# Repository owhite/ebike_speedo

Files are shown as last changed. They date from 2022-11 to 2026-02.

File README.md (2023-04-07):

# EBIKE SPEEDOMETER FEATURES
* Completely uninteresting 14 segment LED displays
* Serial data --> board --> BLE to smartphone
* Compatible with [MESC controller](https://github.com/davidmolony/MESC_Firmware)

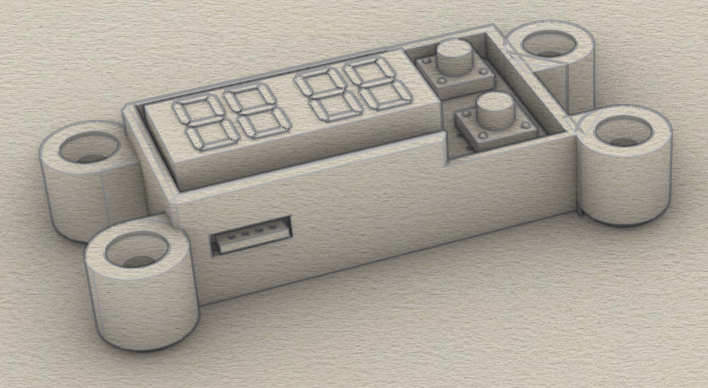
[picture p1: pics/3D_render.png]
3D speedometer


## Operation
Device connects to an ESC (e.g. the [MP2](https://github.com/badgineer/CCC_ESC) with a [F405 pill](https://github.com/davidmolony/F405_pill)) and receives json data via a serial output. Typcial data stream could include:
```
{"amps": 10, "volts": 20, "rpm": 200, "temp": 90}
```
But you can configure the F405 to send other values, but the speedometer is expecting the above tags and ignores others. The speedometer uses these values as ints that will be displayed on the 14 segment LED. RPM will be converted to MPH prior to display. 

Regardless of the values or data structure received, the entired data stream is passed on to a bluetooth device which can be captured on your smartphone using an app like [Serial Bluetooth Terminal](https://play.google.com/store/apps/details?id=de.kai_morich.serial_bluetooth_terminal). 

## Programming
* Use the [STM32CubeIDE](https://www.st.com/en/development-tools/stm32cubeide.html) to progam the microcontroller on the ESC
* Use [platformio](https://platformio.org/) for the ESP32. 

## ESP32 quirks
There are conflicts between bootstrapping capability and usage of some pins. If you notice your board wont program unless you keep the button depressed, it might be due to this conflict.

This reqiures that you burn the flash voltage selection eFuses change the internal regulator’s output voltage to 3.3 V. This was fixed with using a tool from [espressif](https://docs.espressif.com/projects/esptool/en/latest/esp32s3/espefuse/index.html): 

```
$ espefuse.py set_flash_voltage 3.3V --port /dev/cu.usbserial-01562A86
```
be sure to use the appropriate port name. 

## Speedometer operation
* Assemble PCB
* Set the following parameters in ESP32 code:
```
#define POLEPAIRS    5
#define CIRCUMFERENCE 78.5 // circumference in cm of wheel
#define MAXTEMP 65 
// for the range when it provides a percentage
#define MINVOLTAGE 86.4    // lower bound of voltage
#define MAXVOLTAGE 104.0   // 24s lipos fully charge

```
* Upload code to ESP32 using platformio
* Press top button to change LED display
* Display shows: "M", "A", "V" "T" for MPH, amps, battery voltage, and temperature
* Find "ESP32 Speedometer" on your smartphone
* Gather data using an app like [Serial Bluetooth Terminal](https://play.google.com/store/apps/details?id=de.kai_morich.serial_bluetooth_terminal)
* Note on the json data there's a mS value, press lower button to reset to zero

## BOM
* Adafruit Quad Alphanumeric Display w/ backpack
* Adafruit HUZZAH32 – ESP32 Feather Board
* PCB (gerbers are [here](V1.1/gerbers))
* Two 10k 0805 resistors
* [TS14-1212-70-BK-160-SCR-D](https://www.cuidevices.com/product/resource/ts14.pdf) tactile switches
* 0.1 inch spacing header boards
* This [housing](3D_model/speedo_housing.stl) might be useful

Let's play: how tall is your stack of boards!? 
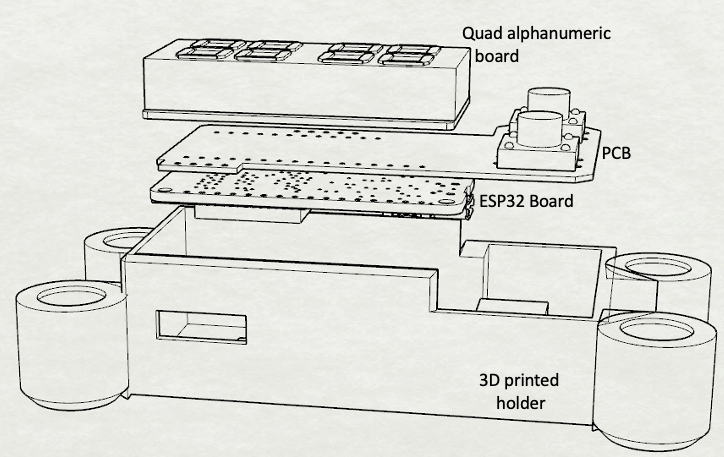
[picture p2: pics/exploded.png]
Separate parts


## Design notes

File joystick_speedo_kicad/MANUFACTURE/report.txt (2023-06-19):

Info: Placement file: '/Users/owhite/kicad/ebike_speedo/speed_joystick/speed_joystick-all-pos.csv'.
Info: Component count: 20.
Info: File generation successful.

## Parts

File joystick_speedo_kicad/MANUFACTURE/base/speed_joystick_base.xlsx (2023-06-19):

Comment | Designator | Footprint | LCSC
10k | R1,R2,R3,R4,R5,R6,R9,R10 | Resistor_SMD:R_0805_2012Metric | C25804
120 | R7 | Resistor_SMD:R_0805_2012Metric | C17437
JS5208 | SW1 | JS5208:SW_JS5208 | C3029619
TJA1050T/CM,118 | U2 | Package_SO:SOIC-8_3.9x4.9mm_P1.27mm | C6952

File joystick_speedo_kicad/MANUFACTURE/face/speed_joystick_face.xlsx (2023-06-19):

Comment | Designator | Footprint | LCSC
0.1uF | C1,C2,C3,C4,C5,C6,C7,C8,C9,C10,C11,C12,C13,C14,C15,C16,C17,C18,C19,C20,C21,C22,C23,C24,C25,C26 | Capacitor_SMD:C_0603_1608Metric | C28233
1uF | C27,C28 | Capacitor_SMD:C_0603_1608Metric | C15849
10uF | C29,C30 | Capacitor_SMD:C_0603_1608Metric | C96446
SK6812 | D1,D2,D3,D4,D5,D6,D7,D8,D9,D10,D11,D12,D13,D14,D15,D16,D17,D18,D19,D20,D21,D22,D23,D24 | LED_SMD:LED-SMD_4P-L4.0-W1.6-L | C2890037
100k | R8 | Resistor_SMD:R_0805_2012Metric | C25803
TXS0108E | U3 | Package_SO:TSSOP-20_4.4x6.5mm_P0.65mm | C17206
XC6206PxxxMR | U4 | Package_TO_SOT_SMD:SOT-23 | C5446

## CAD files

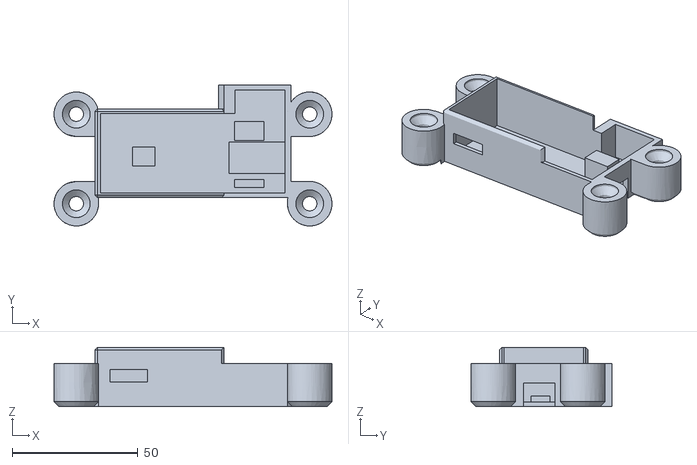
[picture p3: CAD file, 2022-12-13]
3D_model/speedo_housing.stl
110.8 x 56.2 x 23.7

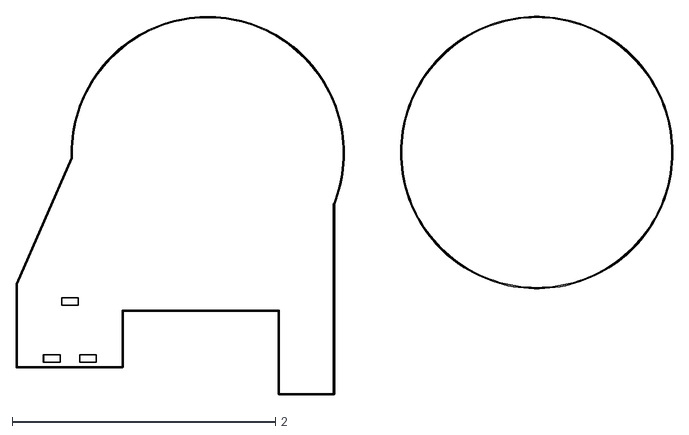
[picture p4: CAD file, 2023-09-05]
joystick_speedo_kicad/DXFs/speed_joystick-Edge_Cuts.dxf
4.99 x 2.87

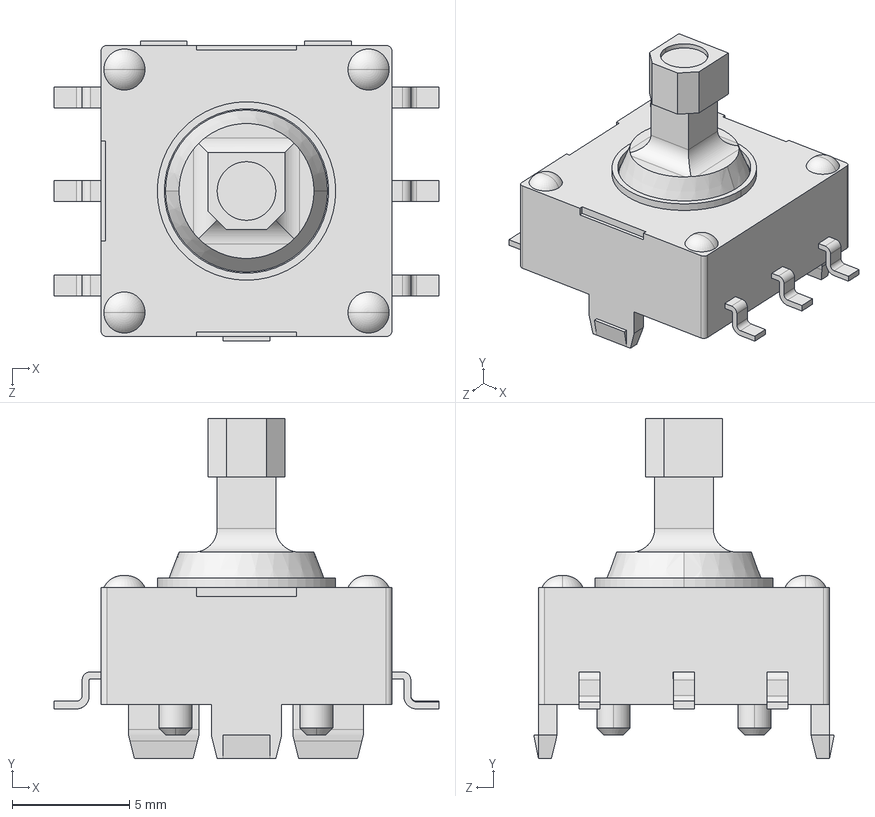
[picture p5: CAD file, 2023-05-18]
mechanical_speedo/JS5208/JS5208.step
16.4 x 14.5 x 12.8 mm

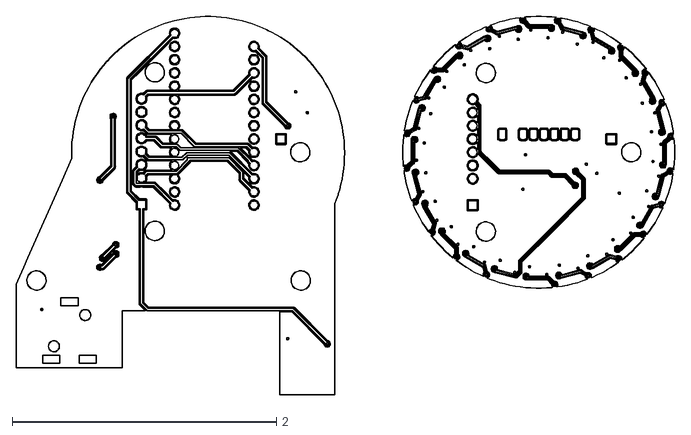
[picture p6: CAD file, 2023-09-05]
joystick_speedo_kicad/DXFs/speed_joystick-B_Cu.dxf
4.98 x 2.86

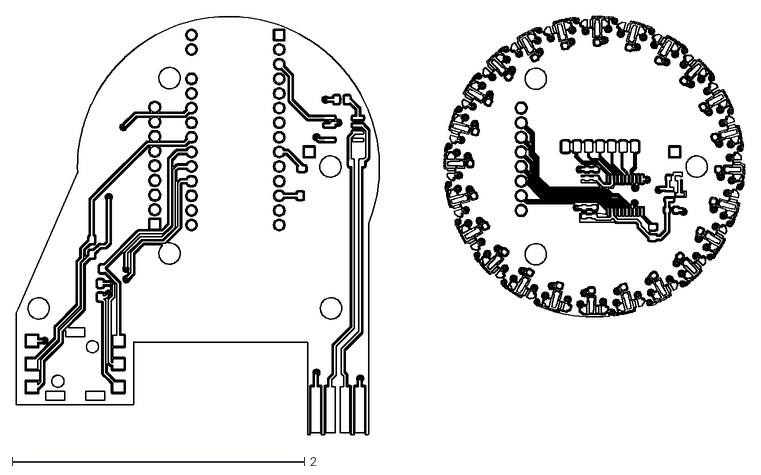
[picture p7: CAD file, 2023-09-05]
joystick_speedo_kicad/DXFs/speed_joystick-F_Cu.dxf
4.98 x 2.86

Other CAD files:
joystick_speedo_kicad/DXFs/speed_joystick-B_Mask.dxf
joystick_speedo_kicad/DXFs/speed_joystick-B_Paste.dxf
joystick_speedo_kicad/DXFs/speed_joystick-B_Silkscreen.dxf
joystick_speedo_kicad/DXFs/speed_joystick-F_Mask.dxf
joystick_speedo_kicad/DXFs/speed_joystick-F_Paste.dxf
joystick_speedo_kicad/DXFs/speed_joystick-F_Silkscreen.dxf

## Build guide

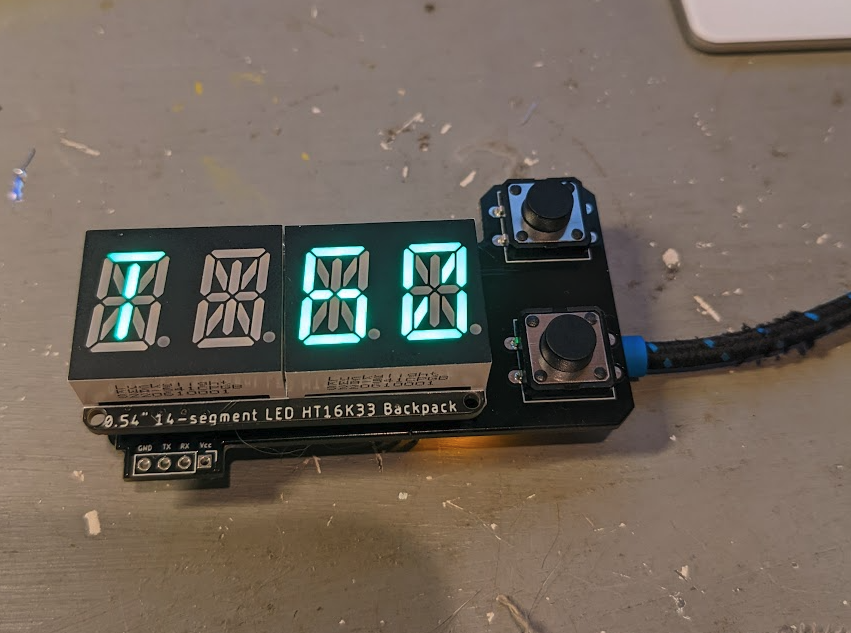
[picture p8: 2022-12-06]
pics/assembled.png

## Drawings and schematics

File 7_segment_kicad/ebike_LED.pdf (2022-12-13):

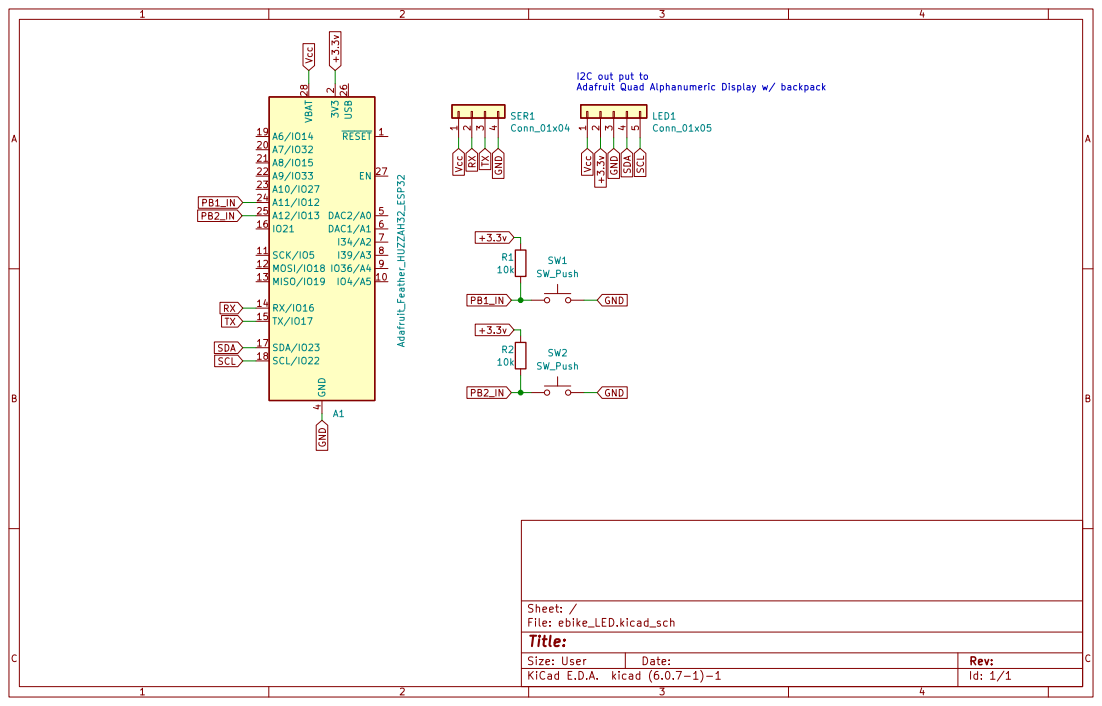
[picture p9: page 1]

I2C out put to
Adafruit Quad Alphanumeric Display w/ backpack

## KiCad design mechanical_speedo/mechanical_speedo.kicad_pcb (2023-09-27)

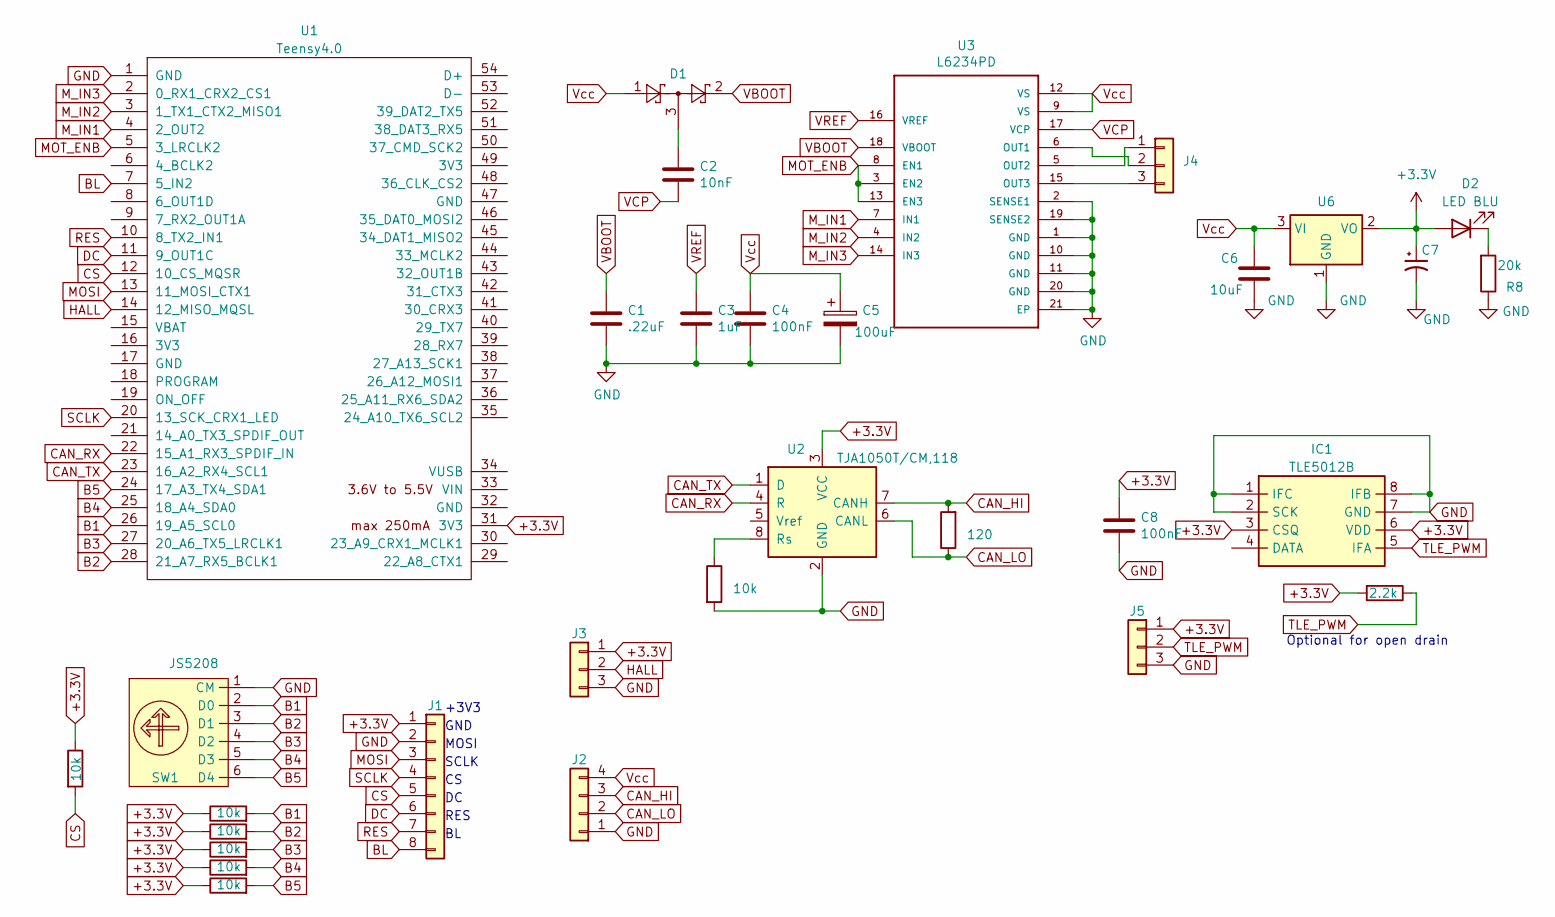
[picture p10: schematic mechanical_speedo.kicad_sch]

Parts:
C1: .22uF; C_0805_2012Metric; LCSC C5378
C2: 10nF; C_0603_1608Metric; LCSC C57112
C3: 1uF; C_0805_2012Metric; LCSC C28323
C4, C8: 100nF; C_0603_1608Metric; LCSC C14663
C5: 100uF; CP_EIA-3528-21_Kemet-B; LCSC C16133
C6: 10uF; C_0805_2012Metric; LCSC C15850
C7: C_Polarized_Small_US; CP_EIA-3216-18_Kemet-A; LCSC C7171
D1: BAT54S; SOT-23; LCSC C19726
D2: LED BLU; LED_0603_1608Metric; LCSC C72041
IC1: TLE5012B; SOIC127P600X175-8N; Mouser Part Number 726-TLE5012BE5000X
J1: Conn_01x08; 8_hole
J2: Conn_01x04; my_4_tab_edge
J3, J4, J5: Conn_01x03; PinHeader_1x03_P2.54mm_Vertical
R1, R2, R3, R4, R5, R6, R9: 10k; R_0805_2012Metric; LCSC C25804
R7: 120; R_0805_2012Metric; LCSC C17437
R8: 20k; R_0603_1608Metric; LCSC C4184
R11: 2.2k; R_0603_1608Metric; LCSC C4184
SW1: JS5208; SW_JS5208; LCSC C3029619
U1: Teensy4.0; Teensy32
U2: TJA1050T/CM,118; SOIC-8_3.9x4.9mm_P1.27mm; LCSC C6952
U3: L6234PD
U6: LD1117S18TR_SOT223; SOT-223-3_TabPin2; LCSC C2984862

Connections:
+3.3V: C7.1, C8.1, D2.2 (A), IC1.3 (CSQ), IC1.6 (VDD), J1.1, J3.1, J5.1, R1.1, R2.1, R4.1, R5.1, R6.1, R9.1, R11.2, U1.31 (3V3), U2.3 (VCC), U6.2 (VO)
B1: R6.2, SW1.2 (D0), U1.26 (19_A5_SCL0)
B2: R5.2, SW1.3 (D1), U1.28 (21_A7_RX5_BCLK1)
B3: R4.2, SW1.4 (D2), U1.27 (20_A6_TX5_LRCLK1)
B4: R2.2, SW1.5 (D3), U1.25 (18_A4_SDA0)
B5: R1.2, SW1.6 (D4), U1.24 (17_A3_TX4_SDA1)
BL: J1.8, U1.7 (5_IN2)
CAN_HI: J2.3, R7.2, U2.7 (CANH)
CAN_LO: J2.2, R7.1, U2.6 (CANL)
CAN_RX: U1.22 (15_A1_RX3_SPDIF_IN), U2.4 (R)
CAN_TX: U1.23 (16_A2_RX4_SCL1), U2.1 (D)
CS: J1.5, R9.2, U1.12 (10_CS_MQSR)
DC: J1.6, U1.11 (9_OUT1C)
GND: C1.2, C3.2, C4.2, C5.2, C6.2, C7.2, C8.2, IC1.1 (IFC), IC1.2 (SCK), IC1.7 (GND), IC1.8 (IFB), J1.2, J2.1, J3.3, J5.3, R3.2, R8.1, SW1.1 (CM), U1.1 (GND), U2.2 (GND), U3.1 (GND), U3.2 (SENSE1), U3.10 (GND), U3.11 (GND), U3.19 (SENSE2), U3.20 (GND), U3.21 (EP), U6.1 (GND)
HALL: J3.2, U1.14 (12_MISO_MQSL)
MOSI: J1.3, U1.13 (11_MOSI_CTX1)
MOT_ENB: U1.5 (3_LRCLK2), U3.3 (EN2), U3.8 (EN1), U3.13 (EN3)
M_IN1: U1.4 (2_OUT2), U3.7 (IN1)
M_IN2: U1.3 (1_TX1_CTX2_MISO1), U3.4 (IN2)
M_IN3: U1.2 (0_RX1_CRX2_CS1), U3.14 (IN3)
unnamed: C2.1, D1.3
unnamed: D2.1 (K), R8.2
unnamed: J4.1, U3.5 (OUT2)
unnamed: J4.2, U3.6 (OUT1)
unnamed: J4.3, U3.15 (OUT3)
unnamed: R3.1, U2.8 (Rs)
RES: J1.7, U1.10 (8_TX2_IN1)
SCLK: J1.4, U1.20 (13_SCK_CRX1_LED)
TLE_PWM: IC1.5 (IFA), J5.2, R11.1
VBOOT: C1.1, D1.2, U3.18 (VBOOT)
VCP: C2.2, U3.17 (VCP)
VREF: C3.1, U3.16 (VREF)
Vcc: C4.1, C5.1, C6.1, D1.1, J2.4, U3.9 (VS), U3.12 (VS), U6.3 (VI)

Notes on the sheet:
MOSI
Optional for open drain
RES
GND
+3V3
SCLK

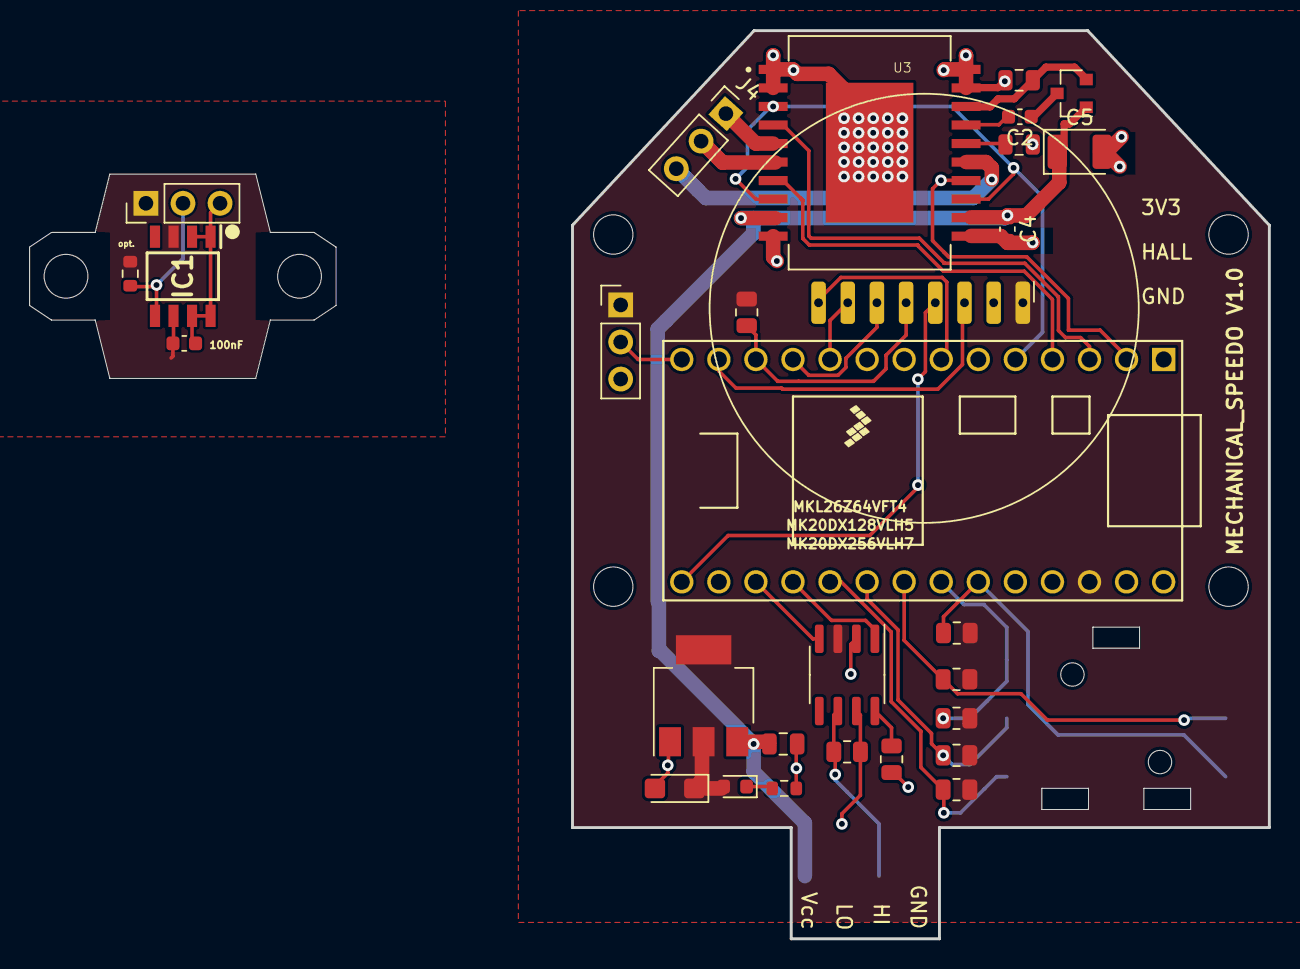
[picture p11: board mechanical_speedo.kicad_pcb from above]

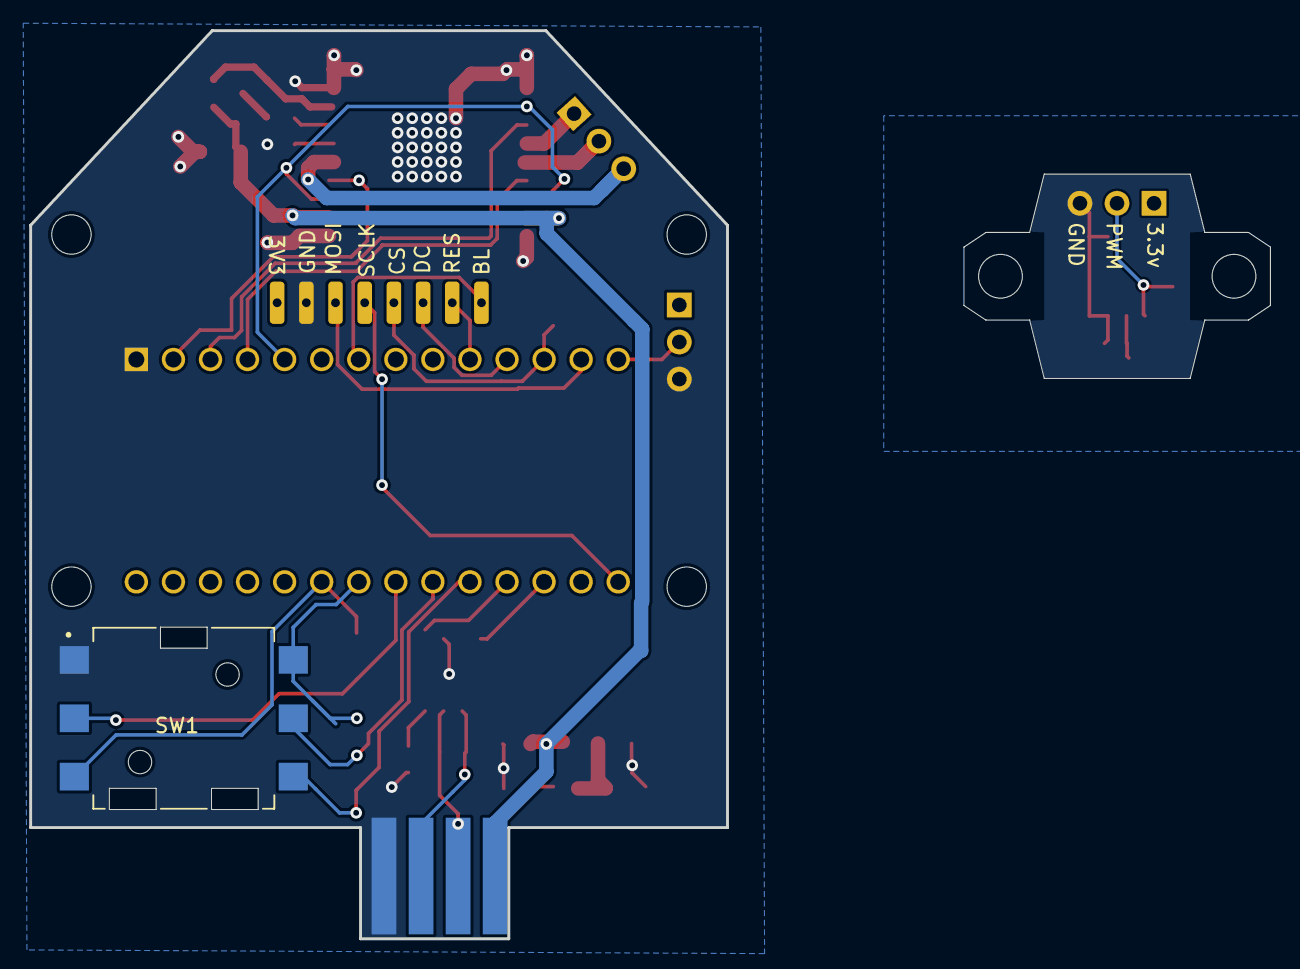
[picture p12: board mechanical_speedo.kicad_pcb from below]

Board: 2 copper layers, 47.8 x 62.2 mm, 31 parts (2 on the bottom side), 33 nets.

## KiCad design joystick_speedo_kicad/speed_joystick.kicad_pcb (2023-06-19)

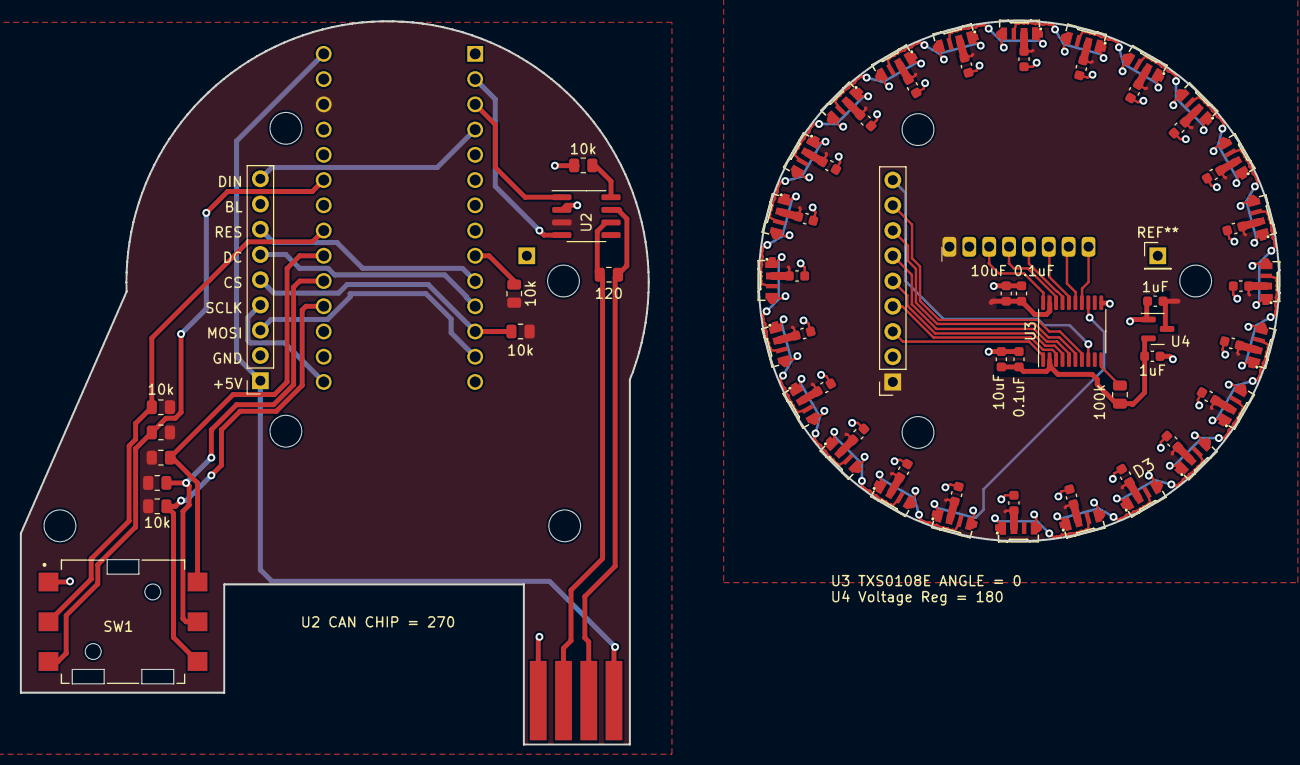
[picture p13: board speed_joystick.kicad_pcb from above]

Board: 2 copper layers, 52.4 x 52.4 mm, 73 parts (1 on the bottom side), 62 nets.

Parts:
C1, C2, C3, C4, C5, C6, C7, C8, C9, C10, C11, C12, C13, C14, C15, C16, C17, C18, C19, C20, C21, C22, C23, C24, C25, C26: 0.1uF; C_0603_1608Metric
C27, C28: 1uF; C_0603_1608Metric
C29, C30: 10uF; C_0603_1608Metric
D1, D2, D3, D4, D5, D6, D7, D8, D9, D10, D11, D12, D13, D14, D15, D16, D17, D18, D19, D20, D21, D22, D23, D24: SK6812; LED-SMD_4P-L4.0-W1.6-L
J1: Conn_01x08; 8_hole
J2: Conn_01x04; my_4_tab_edge
J3, J4: Conn_01x09; PinSocket_1x09_P2.54mm_Vertical
R1, R2, R3, R4, R5, R6, R9, R10: 10k; R_0805_2012Metric
R7: 120; R_0805_2012Metric
R8: 100k; R_0805_2012Metric
SW1: JS5208; SW_JS5208
U1: Teensy3.2; Teensy32
U2: TJA1050T/CM,118; SOIC-8_3.9x4.9mm_P1.27mm
U3: TXS0108E; TSSOP-20_4.4x6.5mm_P0.65mm
U4: XC6206PxxxMR; SOT-23

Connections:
+3.3V: R1.1, R2.1, R4.1, R5.1, R6.1, R9.1, R10.1, U1.31 (3.3V), U2.3 (VCC)
+5V: J2.4, J4.1, U1.33 (Vin)
B1: R6.2, SW1.2 (D0), U1.26 (19_A5_SCL0_Touch)
B2: R5.2, SW1.3 (D1), U1.28 (21_A7_RX1_CS_PWM)
B3: R4.2, SW1.4 (D2), U1.25 (18_A4_SDA0_Touch)
B4: R2.2, SW1.5 (D3), U1.24 (17_A3_SDA0_Touch)
B5: R1.2, SW1.6 (D4), U1.23 (16_A2_SCL0_Touch)
BL: J4.8, U1.7 (5_TX1_PWM)
CAN_HI: J2.3, R7.2, U2.7 (CANH)
CAN_LO: J2.2, R7.1, U2.6 (CANL)
CAN_RX: U1.2 (0_RX1_Touch), U2.4 (R)
CAN_TX: U1.3 (1_TX1_Touch), U2.1 (D)
CS1: J4.5, R9.2, U1.12 (10_TX2_CS_PWM)
CS2: R10.2, U1.9 (7_RX3_DOUT)
DC: J4.6, U1.11 (9_RX2_CS_PWM)
DIN: J4.9, U1.4 (2)
DIN_SIG: D24.1 (DIN), U3.13 (B7)
GND: J2.1, J4.2, R3.2, SW1.1 (CM), U1.1 (GND), U2.2 (GND)
MOSI: J4.3, U1.13 (11_DOUT)
unnamed: D1.1 (DIN), D2.3 (DOUT)
unnamed: D2.1 (DIN), D3.3 (DOUT)
unnamed: D3.1 (DIN), D4.3 (DOUT)
unnamed: D4.1 (DIN), D5.3 (DOUT)
unnamed: D5.1 (DIN), D6.3 (DOUT)
unnamed: D6.1 (DIN), D7.3 (DOUT)
unnamed: D7.1 (DIN), D8.3 (DOUT)
unnamed: D8.1 (DIN), D9.3 (DOUT)
unnamed: D10.1 (DIN), D11.3 (DOUT)
unnamed: D9.1 (DIN), D10.3 (DOUT)
unnamed: D11.1 (DIN), D12.3 (DOUT)
unnamed: D12.1 (DIN), D13.3 (DOUT)
unnamed: D13.1 (DIN), D14.3 (DOUT)
unnamed: D14.1 (DIN), D15.3 (DOUT)
unnamed: D15.1 (DIN), D16.3 (DOUT)
unnamed: D16.1 (DIN), D17.3 (DOUT)
unnamed: D17.1 (DIN), D18.3 (DOUT)
unnamed: D18.1 (DIN), D19.3 (DOUT)
unnamed: D19.1 (DIN), D20.3 (DOUT)
unnamed: D20.1 (DIN), D21.3 (DOUT)
unnamed: D21.1 (DIN), D22.3 (DOUT)
unnamed: D22.1 (DIN), D23.3 (DOUT)
unnamed: D23.1 (DIN), D24.3 (DOUT)
unnamed: J1.3, U3.20 (B1)
unnamed: J1.4, U3.18 (B2)
unnamed: J1.5, U3.17 (B3)
unnamed: J1.6, U3.16 (B4)
unnamed: J1.7, U3.15 (B5)
unnamed: J1.8, U3.14 (B6)
unnamed: R3.1, U2.8 (Rs)
unnamed: R8.2, U3.10 (OE)
RES: J4.7, U1.10 (8_TX3_DIN)
R_+3.3V: C25.1, C27.1, C30.1, R8.1, U3.2 (VCCA), U4.2 (VO)
R_+5V: C1.1, C2.1, C3.1, C4.1, C5.1, C6.1, C7.1, C8.1, C9.1, C10.1, C11.1, C12.1, C13.1, C14.1, C15.1, C16.1, C17.1, C18.1, C19.1, C20.1, C21.1, C22.1, C23.1, C24.1, C26.1, C28.1, C29.1, D1.2 (VDD), D2.2 (VDD), D3.2 (VDD), D4.2 (VDD), D5.2 (VDD), D6.2 (VDD), D7.2 (VDD), D8.2 (VDD), D9.2 (VDD), D10.2 (VDD), D11.2 (VDD), D12.2 (VDD), D13.2 (VDD), D14.2 (VDD), D15.2 (VDD), D16.2 (VDD), D17.2 (VDD), D18.2 (VDD), D19.2 (VDD), D20.2 (VDD), D21.2 (VDD), D22.2 (VDD), D23.2 (VDD), D24.2 (VDD), J1.1, J3.1, U3.19 (VCCB), U4.3 (VI)
R_BL: J3.8, U3.7 (A6)
R_CS: J3.5, U3.4 (A3)
R_DC: J3.6, U3.5 (A4)
R_DIN: J3.9, U3.8 (A7)
R_GND: C1.2, C2.2, C3.2, C4.2, C5.2, C6.2, C7.2, C8.2, C9.2, C10.2, C11.2, C12.2, C13.2, C14.2, C15.2, C16.2, C17.2, C18.2, C19.2, C20.2, C21.2, C22.2, C23.2, C24.2, C25.2, C26.2, C27.2, C28.2, C29.2, C30.2, D1.4 (VSS), D2.4 (VSS), D3.4 (VSS), D4.4 (VSS), D5.4 (VSS), D6.4 (VSS), D7.4 (VSS), D8.4 (VSS), D9.4 (VSS), D10.4 (VSS), D11.4 (VSS), D12.4 (VSS), D13.4 (VSS), D14.4 (VSS), D15.4 (VSS), D16.4 (VSS), D17.4 (VSS), D18.4 (VSS), D19.4 (VSS), D20.4 (VSS), D21.4 (VSS), D22.4 (VSS), D23.4 (VSS), D24.4 (VSS), J1.2, J3.2, U3.11 (GND), U4.1 (GND)
R_MOSI: J3.3, U3.1 (A1)
R_RES: J3.7, U3.6 (A5)
R_SCLK: J3.4, U3.3 (A2)
SCLK: J4.4, U1.20 (13_LED_SCK)

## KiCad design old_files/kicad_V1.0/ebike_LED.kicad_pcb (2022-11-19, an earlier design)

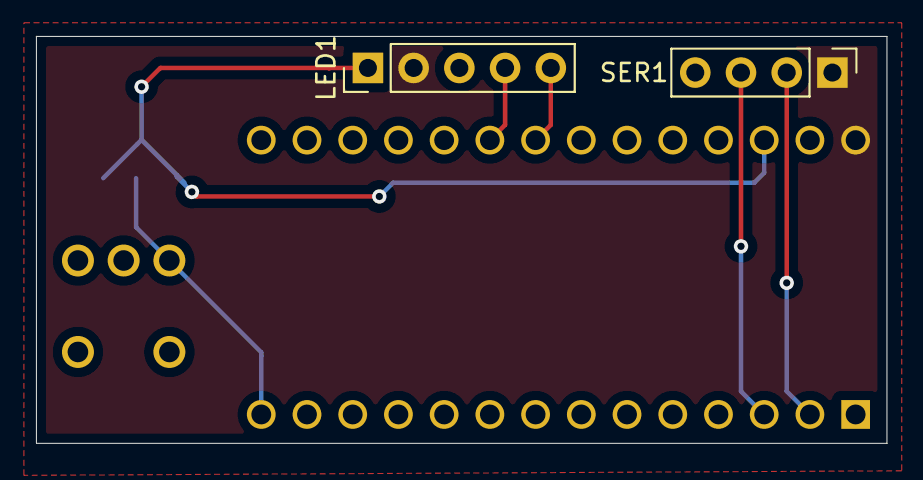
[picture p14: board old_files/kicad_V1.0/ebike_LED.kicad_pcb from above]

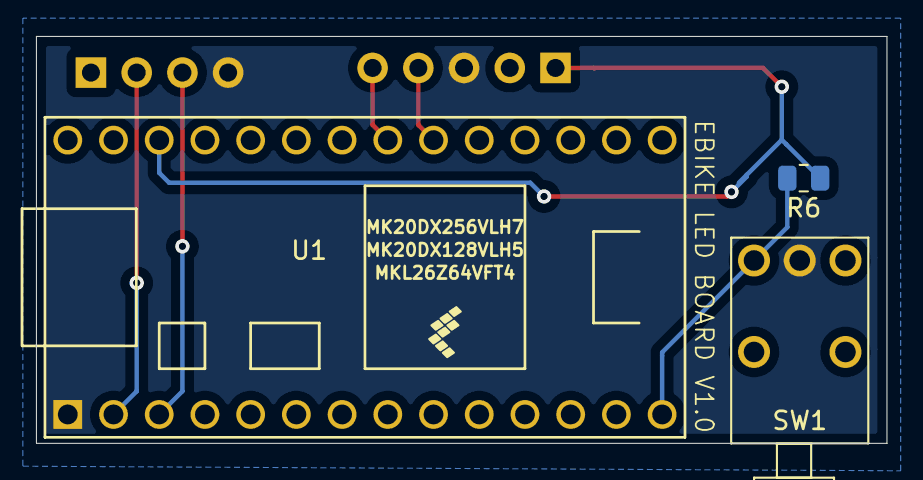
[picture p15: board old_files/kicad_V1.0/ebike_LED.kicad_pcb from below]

Board: 2 copper layers, 47.2 x 22.6 mm, 5 parts (3 on the bottom side), 8 nets.

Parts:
LED1: Conn_01x05; PinHeader_1x05_P2.54mm_Vertical
R6: 10k; R_0805_2012Metric
SER1: Conn_01x04; PinHeader_1x04_P2.54mm_Vertical
SW1: Conn_01x02; my_pushbutton
U1: Teensy3.2; Teensy32

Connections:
+3.3v: LED1.1, R6.1, U1.31
GND: LED1.3, SER1.4, SW1.2, U1.1
PB1_IN: R6.2, SW1.1, U1.14
Rx-BESC: SER1.3, U1.3
SCL: LED1.5, U1.26
SDA: LED1.4, U1.25
Tx-BESC: SER1.2, U1.2
Vcc: LED1.2, SER1.1, U1.33

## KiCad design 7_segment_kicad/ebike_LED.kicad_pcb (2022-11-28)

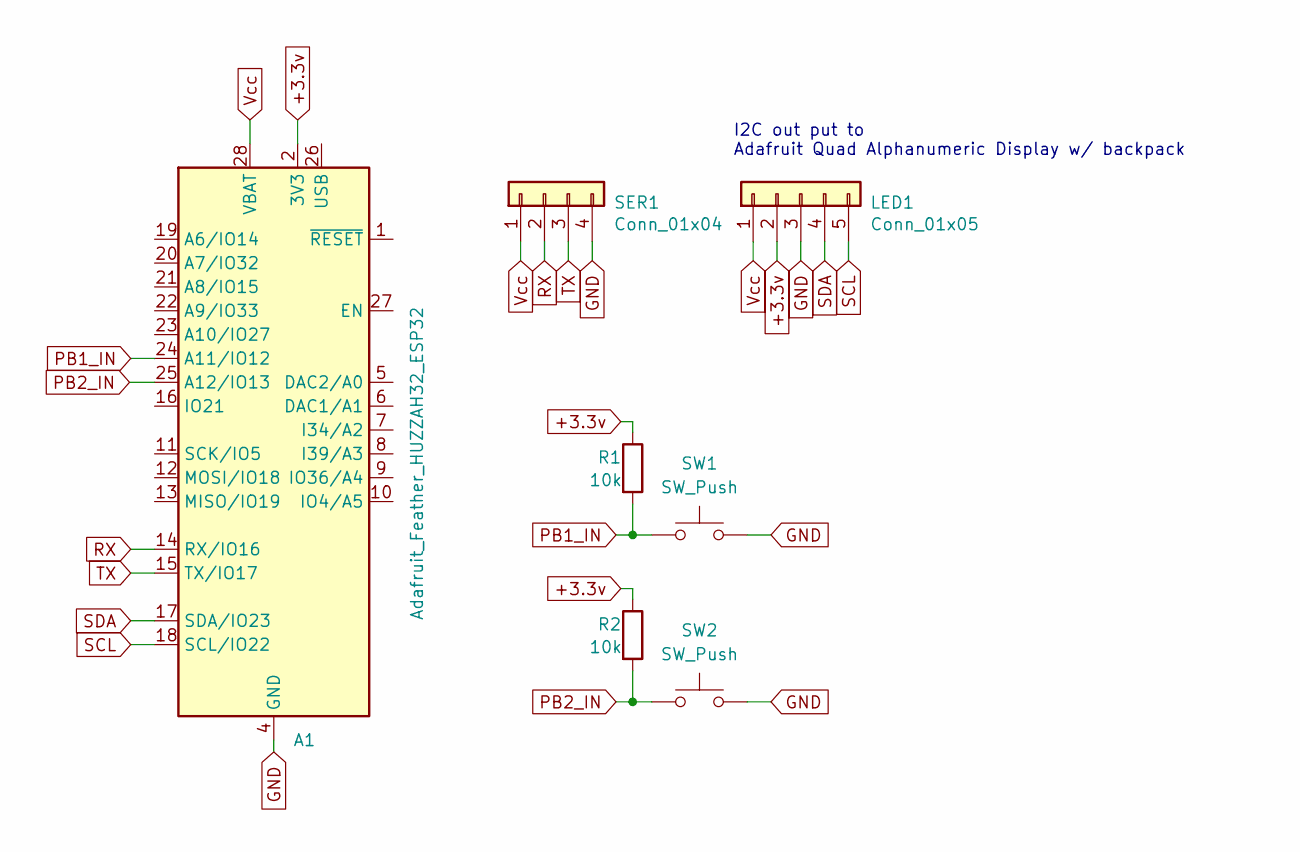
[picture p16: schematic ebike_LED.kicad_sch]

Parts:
A1: Adafruit_Feather_HUZZAH32_ESP32; Adafruit_Feather
LED1: Conn_01x05; PinHeader_1x05_P2.54mm_Vertical
R1, R2: 10k; R_0805_2012Metric
SER1: Conn_01x04; PinHeader_1x04_P2.54mm_Vertical
SW1, SW2: SW_Push; SW_PUSH-12mm

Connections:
+3.3v: A1.2 (3V3), LED1.2, R1.1, R2.1
GND: A1.4 (GND), LED1.3, SER1.4, SW1.2, SW2.2
PB1_IN: A1.24 (A11/IO12), R1.2, SW1.1
PB2_IN: A1.25 (A12/IO13), R2.2, SW2.1
RX: A1.14 (RX/IO16), SER1.2
SCL: A1.18 (SCL/IO22), LED1.5
SDA: A1.17 (SDA/IO23), LED1.4
TX: A1.15 (TX/IO17), SER1.3
Vcc: A1.28 (VBAT), LED1.1, SER1.1

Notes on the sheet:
I2C out put to Adafruit Quad Alphanumeric Display w/ backpack

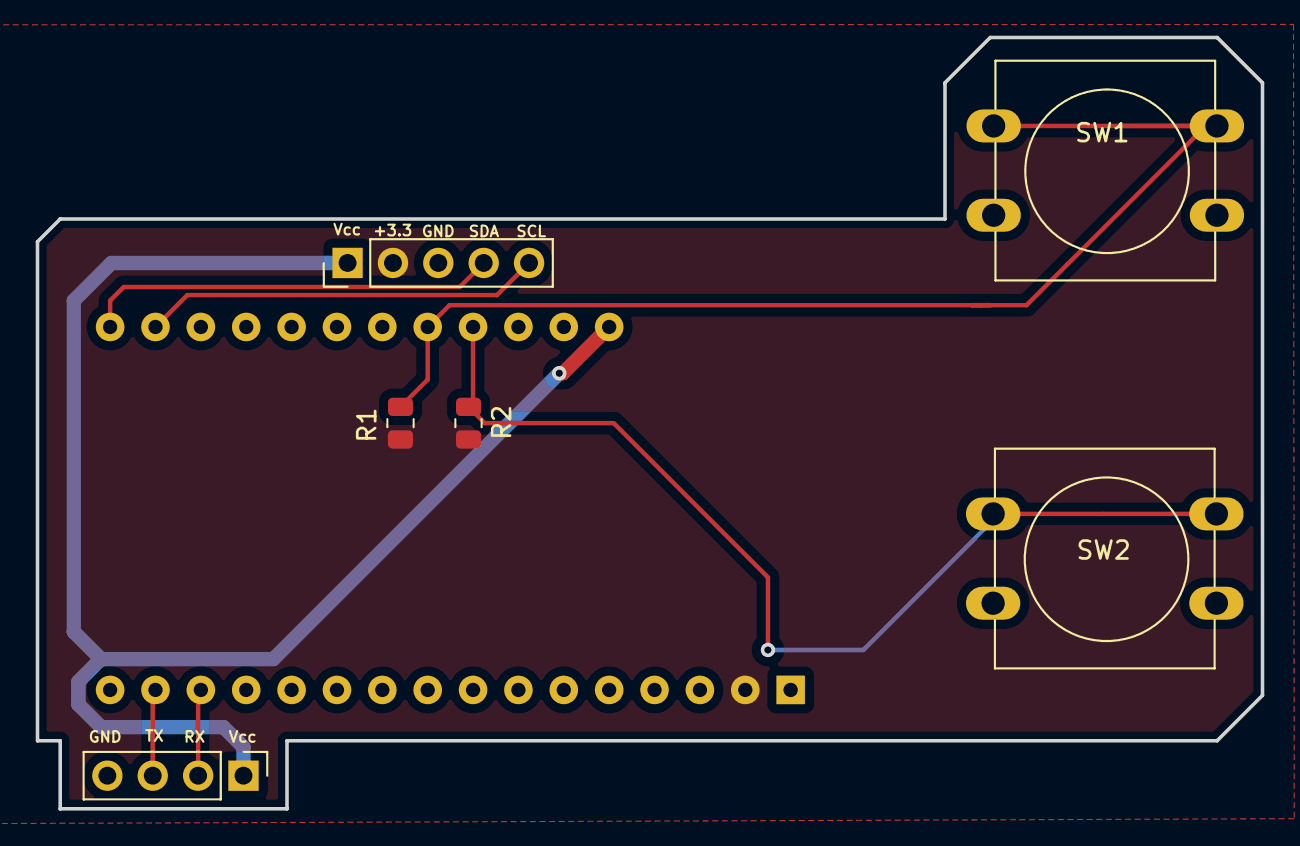
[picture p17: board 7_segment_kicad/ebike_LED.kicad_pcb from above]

Board: 2 copper layers, 68.6 x 43.2 mm, 7 parts (1 on the bottom side), 9 nets.

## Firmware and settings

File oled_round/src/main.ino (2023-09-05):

// Libraries required to make this thing run.
//  respect all licensing associated with these libraries:
#include <FlexCAN_T4.h>
#include <MenuSystem.h> 
#include <Adafruit_GFX.h>
#include <Adafruit_GC9A01A.h>
#include <Adafruit_NeoPixel.h>
#include <DigiFont.h>
#include <EEPROM.h>
// Other custom code blocks
#include <display_handling.h> // my collection of stupid things
#include <menu_handling.h>
#include <bitmaps.h>
#include <MESCerror.h>
#include <states.h>
#include <can_ids.h> // from Jens' code

// BIKE setup, no I'm not storing all this in eeprom
#define BIKE_SPEED_MAX 50
#define POLEPAIRS    7
#define CIRCUMFERENCE 219.5 
#define GEAR_RATIO 9.82
#define CM_IN_MILE 160900
#define MINVOLTAGE 40.0
#define MAXVOLTAGE 60.0
#define MAXTEMP 70
#define MAXSPEED 50
float EHZ_SCALE_M = (CIRCUMFERENCE * 60 * 60) / (CM_IN_MILE * GEAR_RATIO * POLEPAIRS);
float EHZ_SCALE_K = (CIRCUMFERENCE * 60 * 60) / (100000 * GEAR_RATIO * POLEPAIRS);

// eeprom storage positions
#define RESET_STORED_VALUES 0x0000 // change to 1 if store new values
#define PIX_BRIGHTNESS_ADDR 0x0011
#define PIX_COLOR_ADDR      0x0012
#define DISPLAY_STATE_ADDR  0x0013
#define METRIC_PREF_ADDR    0x0014

// joystick button setup
const uint8_t btnMax = 5;
elapsedMillis elapsedBtnTime[btnMax] = {elapsedMillis(), elapsedMillis(), elapsedMillis(), elapsedMillis(), elapsedMillis()};
uint16_t btnDelay = 50;
boolean btnPressed[] = {false, false, false, false, false};
uint8_t btnPin[5] = {19, 21, 18, 17, 16};
uint8_t btnNum = 0;

// neopixel setup
#define PIXELPIN   2
#define NUMPIXELS 24
Adafruit_NeoPixel ring(NUMPIXELS, PIXELPIN, NEO_GRB + NEO_KHZ800);

const uint8_t PIX_RED   = 0;
const uint8_t PIX_GREEN = 1;
const uint8_t PIX_BLUE  = 2;
const uint8_t PIX_WHITE = 3; 

uint32_t colorArray[] = {ring.Color(255, 0, 0), ring.Color(0, 255, 0), ring.Color(0, 0, 255), ring.Color(255, 255, 255)};

// gets changed later by eepromDefaultValues();
uint8_t metric_pref = 0;
uint8_t pixelColor = PIX_WHITE;
uint8_t neoBrightVal = 5;

// round oled setup
//  see Adafruit_GC9A01A github for pin usage
#define LCD_BL_PIN 5 // pin used for brightness
Adafruit_GC9A01A lcd(10, 9, 11, 13, 8, 12);

// CAN stuff
#define CAN_PACKET_SIZE  8

FlexCAN_T4<CAN2, RX_SIZE_256, TX_SIZE_16> can;
CAN_message_t msg;
unsigned long canReceiveTime;
const unsigned long canInterval = 2000;
uint8_t canBuf[8] = {};
const uint8_t userRequestMax = 5; 
float reportedValue; 
float reportValues[userRequestMax] = {};
bool canFlag = false;
bool errorFlag = false;
bool canFlag_old = false;
bool errorFlag_old = false;

// Digifont setup, set up here but used in displayHandlder object. 
void customLineH(int x0,int x1, int y, int c)    { lcd.drawFastHLine(x0,y,x1-x0+1,c); }
void customLineV(int x, int y0,int y1, int c)    { lcd.drawFastVLine(x,y0,y1-y0+1,c); } 
void customRect(int x, int y,int w,int h, int c) { lcd.fillRect(x,y,w,h,c); } 
DigiFont font(customLineH, customLineV, customRect);

// display things
int input_state = INPUT_MENU;
int state = IDLE_DISPLAY;

displayHandler display;

uint32_t dataInterval = 4000; 
int main_display_state = MAIN_DISPLAY_BAT;
uint8_t brightness_val = 10;
int count = 0;
bool entered_menu = true;
float level_old = 0.0;
float level = 0.8;

// menu setup
MyRenderer my_renderer;
MenuSystem ms(my_renderer);

Menu       mu1    ("Display");
Menu       mu2    ("Errors");
MenuItem   mu3    ("Brightness",   [] { changeState(INIT_BRIGHTNESS); });
Menu       mu4    ("Ring Colors");

MenuItem   mu1_mi1("Amps" , [] { updateMainDisplay(MAIN_DISPLAY_AMPS);  });
MenuItem   mu1_mi2("BAT  ", [] { updateMainDisplay(MAIN_DISPLAY_BAT); });
MenuItem   mu1_mi3("ehz"  , [] { updateMainDisplay(MAIN_DISPLAY_EHZ);   });
MenuItem   mu1_mi4("TEMP" , [] { updateMainDisplay(MAIN_DISPLAY_TEMP);  });
MenuItem   mu1_mi5("MPH"  , [] { updateMainDisplay(MAIN_DISPLAY_MPH);   });
MenuItem   mu1_mi6("KPH"  , [] { updateMainDisplay(MAIN_DISPLAY_KPH);   });
MenuItem   mu1_mi7("FW"   , [] { updateMainDisplay(MAIN_DISPLAY_FW);    });

MenuItem   mu2_mi1("View errors",  [] { changeState(INIT_ERRORS); });
MenuItem   mu2_mi2("Reset errors", &errorReset);

MenuItem   mu4_mi1("RED" ,  [] { changeLEDColor(PIX_RED, "red"); });
MenuItem   mu4_mi2("GREEN", [] { changeLEDColor(PIX_GREEN, "green"); });
MenuItem   mu4_mi3("BLUE",  [] { changeLEDColor(PIX_BLUE, "blue"); });
MenuItem   mu4_mi4("WHITE", [] { changeLEDColor(PIX_WHITE, "white"); });

// menu callbacks
void changeLEDColor(uint32_t color, char *str) {
  Serial.print("LED color :: ");
  Serial.println( color );

  lcd.fillScreen(BLACK);
  lcd.setTextSize(2);
  lcd.setTextColor(WHITE);
  lcd.setCursor(20, 6 * LCD_CHAR_HEIGHT);
  lcd.print("change color:");
  lcd.setCursor(20, 8 * LCD_CHAR_HEIGHT);
  lcd.print(str);
  pixelColor = color;
  updateRingBrightness();

  delay(1000); // pause to look at LCD

  EEPROM.write(PIX_COLOR_ADDR, color);

  display.setupFrame(main_display_state);
  // this used to be false, changing this to see what happens
  // entered_menu = false; 
  entered_menu = true; 
  state = INIT_DISPLAY;
}

void updateMainDisplay(int val) {
  Serial.print("diplay change :: ");
  Serial.println( val );

  lcd.setTextSize(2);
  lcd.setCursor(20, 6 * LCD_CHAR_HEIGHT);
  lcd.setTextColor(WHITE);
  lcd.fillScreen(BLACK);
  lcd.print("set main disp:");
  display.drawRGBBitmap(32, 8 * LCD_CHAR_HEIGHT, bitmap[val], BITMAP_WIDTH, BITMAP_HEIGHT);
  delay(1000); // pause to look at LCD

  main_display_state = val;
  EEPROM.write(DISPLAY_STATE_ADDR, main_display_state);

  display.setupFrame(main_display_state);
  // this used to be false, changing this to see what happens
  // entered_menu = false; 
  entered_menu = true;
  state = INIT_DISPLAY;
}

void changeState(int val) {
  Serial.print("state change :: ");
  Serial.println( val );

  state = val;

  entered_menu = true;

  lcd.setTextSize(1);
  lcd.setCursor(0, 6 * LCD_CHAR_HEIGHT);
  lcd.setTextColor(WHITE);
  // lcd.print("state change: ");
  // lcd.print(state);

  delay(500); // pause to look at LCD
}

// doesnt work yet -- hope to tell MESC to reset the error someday
void errorReset(MenuComponent* p_menu_component) {
  lcd.setTextColor(WHITE);
  lcd.setTextSize(2);
  lcd.setCursor(20, 8 * LCD_CHAR_HEIGHT);
  lcd.print("Error code reset");
  lcd.setCursor(24, 10 * LCD_CHAR_HEIGHT);
  lcd.print("...would be cool");
  Serial.println("Error reset selected");
  state = IDLE_MENU;
}

void setup() {
  Serial.begin(9600);
  can.begin();
  can.setBaudRate(500000);

  eepromDefaultValues();

  pinMode(LCD_BL_PIN, OUTPUT); // LCD brightness
  digitalWrite(LCD_BL_PIN, HIGH);

  lcd.begin();
  lcd.setRotation(0);
  lcd.fillScreen(BLACK);
  lcd.setTextSize(1);

  ring.begin(); 
  ring.setBrightness(neoBrightVal);
  ring.clear();
  ring.show(); // one LED flashes for some reason
  ring.clear();
  ring.show(); 

  for (int i = 0; i < 5; i++) { pinMode(btnPin[i], INPUT); }

  // some parts parts of code change the LCD in the displayHandler
  //  while other parts do it here in main. not clever, but ¯\_(ツ)_/¯
  display.begin(&lcd, &font, &ring);

  display.showStarField();

  state = INIT_DISPLAY;

  my_renderer.initLCD(&lcd);
  ms.get_root_menu().add_menu(&mu1, RENDER_LIST);
  mu1.add_item(&mu1_mi1);
  mu1.add_item(&mu1_mi2);
  mu1.add_item(&mu1_mi3);
  mu1.add_item(&mu1_mi4);
  mu1.add_item(&mu1_mi5);
  mu1.add_item(&mu1_mi6);
  mu1.add_item(&mu1_mi7);

  ms.get_root_menu().add_menu(&mu2, RENDER_LIST);
  mu2.add_item(&mu2_mi1);
  mu2.add_item(&mu2_mi2);

  ms.get_root_menu().add_item(&mu3);

  ms.get_root_menu().add_menu(&mu4, RENDER_LIST);
  mu4.add_item(&mu4_mi1);
  mu4.add_item(&mu4_mi2);
  mu4.add_item(&mu4_mi3);
  mu4.add_item(&mu4_mi4);

  entered_menu = true;
}

void loop() {
  // menu timeout
  state = ((millis() - ms.get_last_menu_time() ) > dataInterval) ? INIT_DISPLAY : state;

  // can timeout
  canFlag = ((millis() - canReceiveTime ) > canInterval) ? true : false;

  level = reportValues[2];

  serial_input();
  can_input();
  joystick();

  switch (state) {
  case INIT_MENU:
    {
      entered_menu = true;
      ms.display();
      state = IDLE_MENU;
      break;
    }
  case INIT_DISPLAY: // decides to repaint display or go to idle_display
    {
      if (entered_menu) {
	display.setupFrame(main_display_state);
	display.updateBattery(reportValues[2], MINVOLTAGE, MAXVOLTAGE);
	entered_menu = false;
      }
      display.updateCANErrorFlags(canFlag, errorFlag);
      // if the user timesouts the menu, menu is reset to top
      input_state = INPUT_MENU;
      ms.reset(); 
      state = IDLE_DISPLAY;
    }
    break;
  case INIT_BRIGHTNESS:
    {
      input_state = INPUT_NUMBER;
      lcd.fillScreen(BLACK);
      lcd.setTextSize(2);
      lcd.setTextColor(WHITE);
      lcd.setCursor(20, 6 * LCD_CHAR_HEIGHT);
      lcd.print("brightness");
      lcd.setCursor(20, 8 * LCD_CHAR_HEIGHT);
      lcd.print("use up/down/back");
      Serial.println("BRIGHT!");
      ring.clear();

      // joystick & serial handlers take it from here
      state = IDLE_MENU;
    }
    break;
  case INIT_ERRORS:
    {
      lcd.fillScreen(BLACK);
      lcd.setTextSize(2);
      int y = 40;

      lcd.setCursor(30, y);
      lcd.setTextColor(WHITE);
      lcd.print("MESC ERRORS:");

      y += 2 * LCD_CHAR_HEIGHT;

      int error_val = 10;

      for(int i=0;i<32;i++) {
	if (error_val & 0x0001) {
	  lcd.setTextSize(2);
	  lcd.setCursor(20, y);
	  y += (2 * LCD_CHAR_HEIGHT);
	  lcd.print(error_codes[i]);
	  Serial.println(error_codes[i]);
	}
	error_val = error_val >> 1;
      }
      state = SHOW_ERRORS;
    }
    break;
  case IDLE_DISPLAY:
    // this updates the important numbers each cycle
    {
      // the big number on the display
      // this is just ehz right now
      int x  = map(sine256[count], 0, 255, 0, 50);
      display.displayNum(x, 36, 30, 60);

      // display.displayNum(reportValues[2], 36, 30, 60);
      // miles
      display.displayNum(0, 9, (1 * LCD_WD / 3) + 8, (2 * LCD_HT / 3) + 18);
      // temp
      display.displayNum(reportValues[4], 9, 30, (2 * LCD_HT / 3) + 18);

      // update battery icon only when needed
      level = reportValues[2];
      if (abs(level - level_old) > .12) { display.updateBattery(level, MINVOLTAGE, MAXVOLTAGE); }
      level_old = level;
      
      display.updateCANErrorFlags(canFlag, errorFlag);

      int speed = (METRIC_PREF_ADDR) ? reportValues[1] * EHZ_SCALE_K : reportValues[1] * EHZ_SCALE_M;
      int pixelPos = scale(speed, 0, MAXSPEED, 0, 20);
      
      // foolin' around to play with pixels
      pixelPos = map(sine256[count], 0, 255, 0, 20);
      // update outer ring
      ring.clear();
      if (reportValues[0] < MAXSPEED) {
	// notice we add one to position
	ring.setPixelColor(1, colorArray[PIX_BLUE]);
	ring.setPixelColor(5, colorArray[PIX_BLUE]);
	ring.setPixelColor(9, colorArray[PIX_BLUE]);
	ring.setPixelColor(13, colorArray[PIX_BLUE]);
	ring.setPixelColor(17, colorArray[PIX_BLUE]);
	ring.setPixelColor(21, colorArray[PIX_BLUE]);
	ring.setPixelColor(1 + pixelPos, colorArray[pixelColor]);
      }
      else {
	ring.setPixelColor(19, PIX_RED); // warn the rider
	ring.setPixelColor(20, PIX_RED);
	ring.setPixelColor(21, PIX_RED);
      }
      ring.show(); 
    }
    break;
  case SHOW_ERRORS: // idle until timeout
  case IDLE_MENU:
    break;
  default:
    break;
  }

  delay(50);
  count += 1;
  if (count > 255) {count = 0;};
}

long scale(long x, long in_min, long in_max, long out_min, long out_max) {
  return (x - in_min) * (out_max - out_min) / (in_max - in_min) + out_min;
}

void updateRingBrightness() {
  for (int i=0; i<NUMPIXELS; i++) {
    ring.setBrightness(neoBrightVal);
    ring.setPixelColor(i, colorArray[pixelColor]);
  }
  ring.show(); 
}

void joystick() {
  for(int i = 0; i < btnMax; i++) {
    if (btnPressed[i] && elapsedBtnTime[i] > btnDelay) {
      elapsedBtnTime[i] = 0;
      btnPressed[i] = false;
      btnNum = i;

      switch (btnNum) {
      case 0: // back
	Serial.println("back"); 
	state = INIT_MENU;
	ms.back();
	break;
      case 1: // select. dont use the "pushdown" button
      case 3: // forward
	Serial.println("select"); 
	if (input_state == INPUT_MENU) {
	  state = INIT_MENU;
	  ms.select();
	}
	if (input_state == INPUT_NUMBER) { } // does nothing
	break;
      case 2: // up
	Serial.println("up");
	if (input_state == INPUT_MENU) {
	  state = INIT_MENU;
	  ms.prev();
	}
	if (input_state == INPUT_NUMBER) {
	  ms.touch();
	  neoBrightVal+=10;
	  if (neoBrightVal > 255) {neoBrightVal = 255;}
	  display.showBrightness(neoBrightVal);
	  updateRingBrightness();
	  EEPROM.write(PIX_BRIGHTNESS_ADDR, neoBrightVal);
	}
	break;
      case 4: // down
	Serial.println("down");
	if (input_state == INPUT_MENU) {
	  state = INIT_MENU;
	  ms.next();
	}
	if (input_state == INPUT_NUMBER) {
	  ms.touch();
	  int inc = 10;
	  if (neoBrightVal <= inc) {
	    inc = 2;
	  }
	  if (neoBrightVal <= inc) {
	    neoBrightVal = 2;
	  }
	  neoBrightVal -= inc;
	  display.showBrightness(neoBrightVal);
	  updateRingBrightness();
	  EEPROM.write(PIX_BRIGHTNESS_ADDR, neoBrightVal);
	}
	break;
      default:
	break;
      }
      delay(200);
    }
    if (digitalRead(btnPin[i]) == LOW && btnPressed[i] == false) {
      Serial.println("start");
      elapsedBtnTime[i] = 0;
      btnPressed[i] = true;
    }
    if (digitalRead(btnPin[i]) == HIGH) {
      btnPressed[i] = false;
    }
  }
}

// this is not CAN input. connect the USB from teensy to computer
//   and use the terminal to test menu. 
void serial_input() { 
  //  there are two menu collection states
  switch (input_state) {
  case INPUT_MENU:
    serial_menu_input();
    break;
  case INPUT_NUMBER:
    serial_brightness_input();
    break;
  default:
    break;
  }
}

/* 
****** keyboard input *******
* w: go to previus item (up)
* s: go to next item (down)
* a: go back (right)
* d: select item
***************
*/

void serial_menu_input() {
  char inChar;
  if((inChar = Serial.read())>0) {
    switch (inChar) {
    case 'w': // Previus item
      state = INIT_MENU;
      ms.prev();
      break;
    case 's': // Next item
      state = INIT_MENU;
      ms.next();
      break;
    case 'a': // Back pressed
      state = INIT_MENU;
      ms.back();
      break;
    case 'd': // Select pressed
      state = INIT_MENU;
      ms.select();
      break;
    default:
      break;
    }
  }
}

/* 
***************
* enable user to change a number
* w: increase number
* s: decrease
* a: go back
* d: do nothin'
***************
*/

void serial_brightness_input() {
  char inChar;
  if((inChar = Serial.read())>0) {
    switch (inChar) {
    case 'w': // Previus item
      Serial.println("ser: up");
      ms.touch();
      neoBrightVal+=10;
      if (neoBrightVal > 255) {neoBrightVal = 255;}
      display.showBrightness(neoBrightVal);
      updateRingBrightness();
      EEPROM.write(PIX_BRIGHTNESS_ADDR, neoBrightVal);
      break;
    case 's': // Next item
      lcd.fillScreen(BLACK);
      Serial.println("ser: down");
      ms.touch();
      neoBrightVal-=10;
      if (neoBrightVal <= 0) {neoBrightVal = 0;}
      display.showBrightness(neoBrightVal);
      updateRingBrightness();
      EEPROM.write(PIX_BRIGHTNESS_ADDR, neoBrightVal);
      break;
    case 'a': // Back pressed
      state = INIT_MENU;
      input_state = INPUT_MENU;
      ms.back();
      break;
    case 'd': // Select pressed
      break;
    case '?':

    default:
      break;
    }
  }
}

void can_input() {
  uint16_t packetId;
  union {
    uint8_t b[4];
    float f;
  } canData1;

  union {
    uint8_t b[4];
    float f;
  } canData2;

  if ( can.read(msg) ) {

    if (msg.len == CAN_PACKET_SIZE) {
      canData1.b[0]=msg.buf[0];
      canData1.b[1]=msg.buf[1];
      canData1.b[2]=msg.buf[2];
      canData1.b[3]=msg.buf[3];
      canData2.b[0]=msg.buf[4];
      canData2.b[1]=msg.buf[5];
      canData2.b[2]=msg.buf[6];
      canData2.b[3]=msg.buf[7];

      if (0) { // debug
	Serial.print("CAN "); 
	Serial.print("MB: "); Serial.print(msg.mb);
	Serial.print("  ID: 0x"); Serial.print(msg.id, HEX );
	Serial.print("  EXT: "); Serial.print(msg.flags.extended );
	Serial.print("  LEN: "); Serial.print(msg.len);
	Serial.print(" DATA: ");
	Serial.print("  TS: "); Serial.println(msg.timestamp);
      }

      packetId = (msg.id >> 16);

      switch (packetId) {
      case CAN_ID_SPEED:
	reportValues[1] = canData1.f;  // ehz
	canReceiveTime = millis();
	break;
      case CAN_ID_BUS_VOLT_CURR:
	reportValues[2] = canData1.f; // battery voltage
	reportValues[3] = canData2.f; // battery current
	reportValues[2] = (reportValues[2] < MINVOLTAGE) ? MINVOLTAGE : reportValues[2];
	canReceiveTime = millis();
	break;
      case CAN_ID_TEMP_MOT_MOS1:
	reportValues[4] = canData2.f;
	canReceiveTime = millis();
	break;
      default:
	break;
      }
    }
  }
}

void eepromDefaultValues() {
  uint8_t value; 
  
  // use this to initialize the teensy or if you create new things to store
  // main_display_state = val;
  if (RESET_STORED_VALUES) { 
    Serial.println("storing values:");
    EEPROM.write(PIX_BRIGHTNESS_ADDR, 125);
    EEPROM.write(PIX_COLOR_ADDR, 3);
    EEPROM.write(METRIC_PREF_ADDR, 0);
    EEPROM.write(DISPLAY_STATE_ADDR, 0);
  }

  Serial.println("getting stored values");
  value = EEPROM.read(PIX_BRIGHTNESS_ADDR);
  Serial.print(PIX_BRIGHTNESS_ADDR);
  Serial.print("\t");  Serial.print(value, DEC);  Serial.println();
  neoBrightVal = value;

  value = EEPROM.read(PIX_COLOR_ADDR);
  Serial.print(PIX_COLOR_ADDR);
  Serial.print("\t");  Serial.print(value, DEC);  Serial.println();
  pixelColor = value;

  value = EEPROM.read(METRIC_PREF_ADDR);
  Serial.print(METRIC_PREF_ADDR);
  Serial.print("\t");  Serial.print(value, DEC);  Serial.println();
  metric_pref = value;

  value = EEPROM.read(DISPLAY_STATE_ADDR);
  Serial.print(DISPLAY_STATE_ADDR);
  Serial.print("\t");  Serial.print(value, DEC);  Serial.println();
  main_display_state = value;
}

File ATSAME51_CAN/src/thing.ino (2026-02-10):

#include <CAN.h>
#include <Wire.h>
#include <Adafruit_GFX.h>
#include <can_ids.h> // from: MESC_Firmware/MESC_RTOS/Tasks/can_ids.h
#include <Adafruit_LEDBackpack.h>
#include "debug.h"
#include <string.h>   // memcpy, strtok
#include <stdlib.h>   // atoi
#include <FlashStorage_SAMD.h>

Adafruit_AlphaNum4 alphaLED = Adafruit_AlphaNum4();

#define BTN_PIN1       12
#define BTN_PIN2       13
#define KILLSWITCH_PIN 17

#define CAN_PACKET_SIZE  8
#define CAN_DEBUG        0

/////////
// bike constants
static const float CIRCUMFERENCE_CM = 219.5f;   // measured with tape
static const float CM_IN_MILE       = 160900.0f;

#define MINVOLTAGE 58
#define MAXVOLTAGE 75
#define MAXTEMP    70

/////////
// Persistent config (Flash)
static const uint16_t CONFIG_MAGIC = 0xB17E;
static const int DEFAULT_POLEPAIRS = 7;

// Your sprockets (given)
static const int DEFAULT_FRONT_SPROCKET = 14;
static const int DEFAULT_BACK_SPROCKET  = 98;

struct PersistConfig {
  uint16_t magic;
  int32_t polepairs;
  int32_t front_sprocket;
  int32_t back_sprocket;
};

FlashStorage(config_storage, PersistConfig);
PersistConfig cfg;

// Runtime (used by math / display)
int   POLEPAIRS_i        = DEFAULT_POLEPAIRS;
int   FRONT_SPROCKET_i   = DEFAULT_FRONT_SPROCKET;
int   BACK_SPROCKET_i    = DEFAULT_BACK_SPROCKET;

float sprocket_ratio_f   = 1.0f;  // Tf/Tb
float mph_per_ehz_scale  = 0.0f;  // multiplier to convert EHz -> mph

static void recalcGearRatioAndScale();
static void loadConfig();
static void saveConfig();

/////////
// CAN variables
unsigned long canReceiveTime = 0;
const unsigned long canInterval = 2000;

uint8_t  canBuf[8] = {};
uint16_t packetId = 0;

float canData1_f = 0.0f;
float canData2_f = 0.0f;

/////////
// reporting things
unsigned long currentTime = 0;
unsigned long reportLastTime = 0;
const unsigned long reportInterval = 800;

const uint8_t prefixes[] = {'M', 'E', 'B', 'A', 'T'};

enum ReportIndex : uint8_t {
  IDX_MPH  = 0,
  IDX_EHZ  = 1,
  IDX_VBUS = 2,
  IDX_IBUS = 3,
  IDX_TEMP = 4,
  IDX_COUNT
};

const uint8_t userRequestMax = IDX_COUNT;

float reportedValue = 0.0f;
float reportValues[IDX_COUNT] = {0};

uint8_t userRequest   = 0; // what the user wants
uint8_t reportInc     = 0; // cycles through things to display
uint8_t lastReportInc = 0;

enum FlagIndex : uint8_t {
  FLAG_CAN_TIMEOUT = 0,
  FLAG_ERROR       = 1,
  FLAG_TEMP        = 2,
  FLAG_COUNT
};

bool flagList[FLAG_COUNT] = {false, false, false}; // can, error, temp

/////////
// button reading timers
const int SHORT_PRESS_TIME = 600;
const int LONG_PRESS_TIME  = 600;

struct ButtonState {
  uint8_t pin;
  int lastState;
  int currentState;
  unsigned long pressedTime;
  unsigned long releasedTime;
};

ButtonState btn1 = { BTN_PIN1, LOW, LOW, 0, 0 };
ButtonState btn2 = { BTN_PIN2, LOW, LOW, 0, 0 };

// control if LED is bright or dim
bool brightnessToggle = true;

static inline void setBrightnessFromToggle() {
  alphaLED.setBrightness(brightnessToggle ? 14 : 0);
}

static inline void clampUserRequest() {
  if (userRequest >= userRequestMax) userRequest = 0;
}

void displayNum3(int n);
void zipDisplay(int c);
uint16_t extract_id(uint32_t ext_id);

void canStatus();
void errorStatus();
void tempStatus();

void handleButton(ButtonState &b);
void onShortPress();
void onLongPress();

///////
// Serial command handling (no Arduino String)
static const uint16_t SERIAL_LINE_MAX = 64;
char serialLine[SERIAL_LINE_MAX];
uint16_t serialLen = 0;

static void pollSerial();
static void handleSerialLine(char *line);
static void printHelp();
static void printConfig();

void setup() {
  Serial.begin(9600);

  // Load persistent values and recalc on boot
  loadConfig();
  recalcGearRatioAndScale();

  pinMode(btn1.pin, INPUT);
  pinMode(btn2.pin, INPUT);

  pinMode(PIN_CAN_STANDBY, OUTPUT);
  pinMode(PIN_CAN_BOOSTEN, OUTPUT);
  digitalWrite(PIN_CAN_STANDBY, false); // standby off
  digitalWrite(PIN_CAN_BOOSTEN, true);  // booster on

  if (!CAN.begin(500000)) {
    DEBUG_PRINTLN("Starting CAN failed!");
    while (1) {}
  }

  CAN.onReceive(onReceive); // register CAN callback

  alphaLED.begin(0x70);
  setBrightnessFromToggle();

  alphaLED.clear();
  alphaLED.writeDigitAscii(1, 'O');
  alphaLED.writeDigitAscii(2, 'F');
  alphaLED.writeDigitAscii(3, 'F');
  alphaLED.writeDisplay();

  btn1.pressedTime = millis();
  btn2.pressedTime = millis();

  zipDisplay(0xBFFF);
  zipDisplay(0xBFFF);
  zipDisplay(0xBFFF);

  // Quick hint at boot
  Serial.println();
  Serial.println("Ready. Type 'H' for help.");
  printConfig();
}

void loop() {
  pollSerial();

  canStatus();
  errorStatus();
  tempStatus();

  // If you want both buttons active, call both:
  // handleButton(btn1);
  handleButton(btn2);

  currentTime = millis();

  // periodic check to change display based on errors
  if ((currentTime - reportLastTime) > reportInterval) {
    lastReportInc = reportInc;

    // reportInc meaning:
    // 0: user display
    // 1: CAN timeout
    // 2: error
    // 3: temp
    int i;
    for (i = (int)lastReportInc + 1; i < 4; i++) {
      if (flagList[i - 1]) { // (1..3) maps to (0..2)
        reportInc = (uint8_t)i;
        break;
      }
    }
    if (i == 4) { reportInc = 0; }

    reportLastTime = currentTime;
  }

  switch (reportInc) {
    case 0: // show what the user wants
      alphaLED.clear();
      alphaLED.writeDigitAscii(0, prefixes[userRequest]);
      displayNum3((int)reportValues[userRequest]); // show on digits 1..3
      alphaLED.writeDisplay();
      reportedValue = reportValues[userRequest];
      break;

    case 1: // show CAN has timed out
      alphaLED.clear();
      alphaLED.writeDigitAscii(1, 'C');
      alphaLED.writeDigitAscii(2, 'A');
      alphaLED.writeDigitAscii(3, 'N');
      alphaLED.writeDisplay();
      break;

    case 2: // show error status
      alphaLED.clear();
      alphaLED.writeDigitAscii(0, 'E');
      displayNum3((int)reportValues[userRequest]); // placeholder until error value is real
      alphaLED.writeDisplay();
      break;

    case 3: // show temp status
      alphaLED.clear();
      alphaLED.writeDigitAscii(0, 'T');
      alphaLED.writeDigitAscii(1, 'E');
      alphaLED.writeDigitAscii(2, 'M');
      alphaLED.writeDigitAscii(3, 'P');
      alphaLED.writeDisplay();
      break;

    default:
      break;
  }
}

void canStatus() {
  flagList[FLAG_CAN_TIMEOUT] = false;
  currentTime = millis();
  if ((currentTime - canReceiveTime) > canInterval) {
    flagList[FLAG_CAN_TIMEOUT] = true;
  }
}

void errorStatus() {
  flagList[FLAG_ERROR] = false;
}

void tempStatus() {
  flagList[FLAG_TEMP] = false;
}
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

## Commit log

2022-11-28 started V1.1
    [ebike_LED-B_Cu.gbr, ebike_LED-B_Mask.gbr, ebike_LED-B_Paste.gbr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]
2022-11-28 gerber generation
    [ebike_LED-B_Cu.gbr, ebike_LED-B_Mask.gbr, ebike_LED-B_Paste.gbr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]
2022-12-06 added esp32 code
2022-12-06 added LED code
2022-12-11 added STM32cube project
2022-12-11 arduino code work
2022-12-13 fixed timer reset
2023-04-03 added kill switch
2023-04-13 broke a bunch of timer issues
    [thing.ino]
2023-04-14 added button press
2023-04-20 minor fixes to CAN values
    [thing.ino]
2023-05-18 added joystick speedo
    [eye_driver-Edge_Cuts.dxf, eye_driver-F_Cu.dxf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]
2023-05-18 pcb work
    [JS5208.step, speed_joystick.kicad_pcb, speed_joystick.kicad_sch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]
2023-05-23 work on speed_joystick pcb
    [eye_driver-Edge_Cuts.dxf, eye_driver-F_Cu.dxf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]
2023-05-31 more round oled work
    [speed_joystick.kicad_sch, untitled.kicad_sch]
2023-06-19 created V1.2
    [speed_joystick.kicad_pcb]
2023-06-19 finalized speed_joystick V1.2
    [PCB_NEW_PCB_2023-06-19.kicad_pcb, speed_joystick.kicad_pcb, speed_joystick.kicad_sch]
2023-06-19 create jlcpcb order
    [speed_joystick-B_Cu.gbr, speed_joystick-B_Mask.gbr, speed_joystick-B_Paste.gbr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]
2023-06-28 rearranged files -> folders
    [JS5208.step, PCB_NEW_PCB_2023-06-19.kicad_pcb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]
2023-09-05 created mechanical_speedo
    [JS5208.step, mechanical_speedo.kicad_pcb, mechanical_speedo.kicad_sch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]
2023-09-19 playing around with motor_test
2023-09-27 added encoder board to mechanical_speedo
    [mechanical_speedo-B_Cu.gbr, mechanical_speedo-B_Mask.gbr, mechanical_speedo-B_Paste.gbr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]
